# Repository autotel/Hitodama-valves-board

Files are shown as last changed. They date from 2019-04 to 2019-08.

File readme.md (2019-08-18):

# to fix:
* ---Teensy-board, connect VCC to teensy 3v---
* ---caps wrong way around in valves boards.---
* ---check about the twistedness of the ribbon cable---

* Cannot use the DAC pins (A21,A22) as digital!

board to control two valves and two pressure sensors from microcontroller.

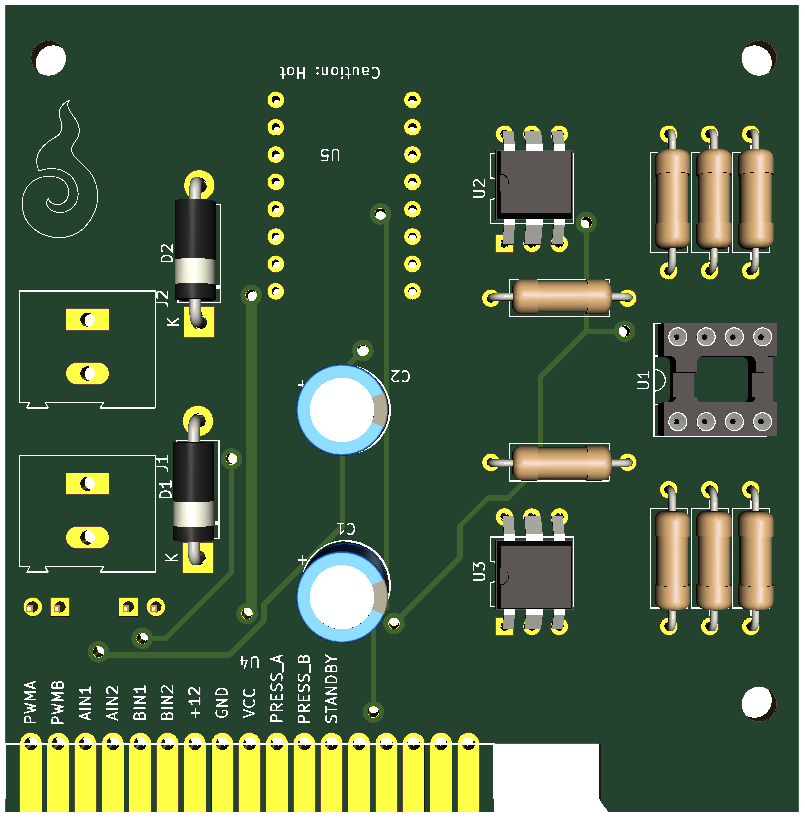
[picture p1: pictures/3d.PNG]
render


Electronic design: Avner Peled & Joaquín Aldunate

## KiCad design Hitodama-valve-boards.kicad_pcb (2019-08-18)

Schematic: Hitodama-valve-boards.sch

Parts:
C1, C2: 100uF 25v; CP_Radial_D8.0mm_P3.80mm
D1, D2: D; D_5W_P12.70mm_Horizontal
H1, H2, H3, H4: MountingHole; MountingHole_3.2mm_M3
J1: Solenoid A; TerminalBlock_Altech_AK300-2_P5.00mm
J2: Solenoid B; TerminalBlock_Altech_AK300-2_P5.00mm
JP1, JP2: (A,B)IN 1; PinHeader_1x02_P2.54mm_Vertical
R1, R5: 80K; R_Axial_DIN0309_L9.0mm_D3.2mm_P12.70mm_Horizontal
R2, R6: 10K; R_Axial_DIN0309_L9.0mm_D3.2mm_P12.70mm_Horizontal
R3, R7: 3.3K; R_Axial_DIN0309_L9.0mm_D3.2mm_P12.70mm_Horizontal
R4, R8: 33K; R_Axial_DIN0309_L9.0mm_D3.2mm_P12.70mm_Horizontal
U1: LM358; DIP-8_W7.62mm_Socket_LongPads
U2: Pressure_b; DIP-6_W10.16mm
U3: Pressure_a; DIP-6_W10.16mm
U4: ChamberBoard_Holder; chamber_board_holder_ 5-5530843-3_male
U5: Pololu-713; pololu713

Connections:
+12V: U4.7, U5.7
/A.IN.1: JP1.1, U4.3, U5.14
/A.IN.2: U4.4, U5.15
/A.PRESSURE: R8.1, U1.1, U4.10
/A.PWM: JP2.2, U4.1, U5.16
/B.IN.1: JP1.2, U4.5, U5.12
/B.IN.2: U4.6, U5.11
/B.PRESSURE: R4.1, U1.7, U4.11
/B.PWM: JP2.1, U4.2, U5.10
/HVA+: D1.1 (K), J1.2, U5.3
/HVA-: D1.2 (A), J1.1, U5.4
/HVB+: D2.1 (K), J2.2, U5.6
/HVB-: D2.2 (A), J2.1, U5.5
/stby: U4.12, U5.13
GND: C1.2, C2.2, R1.1, R5.1, U1.4 (V-), U2.2, U3.2, U4.8, U5.1, U5.9
unnamed: R1.2, R2.2, U1.5 (+)
unnamed: R2.1, U2.4
unnamed: R3.1, R4.2, U1.6 (-)
unnamed: R3.2, U2.1, U2.6
unnamed: R5.2, R6.2, U1.3 (+)
unnamed: R6.1, U3.4
unnamed: R7.1, R8.2, U1.2 (-)
unnamed: R7.2, U3.1, U3.6
VCC: C1.1, C2.1, U1.8 (V+), U2.5, U3.5, U4.9, U5.2

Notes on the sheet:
Modular
Head

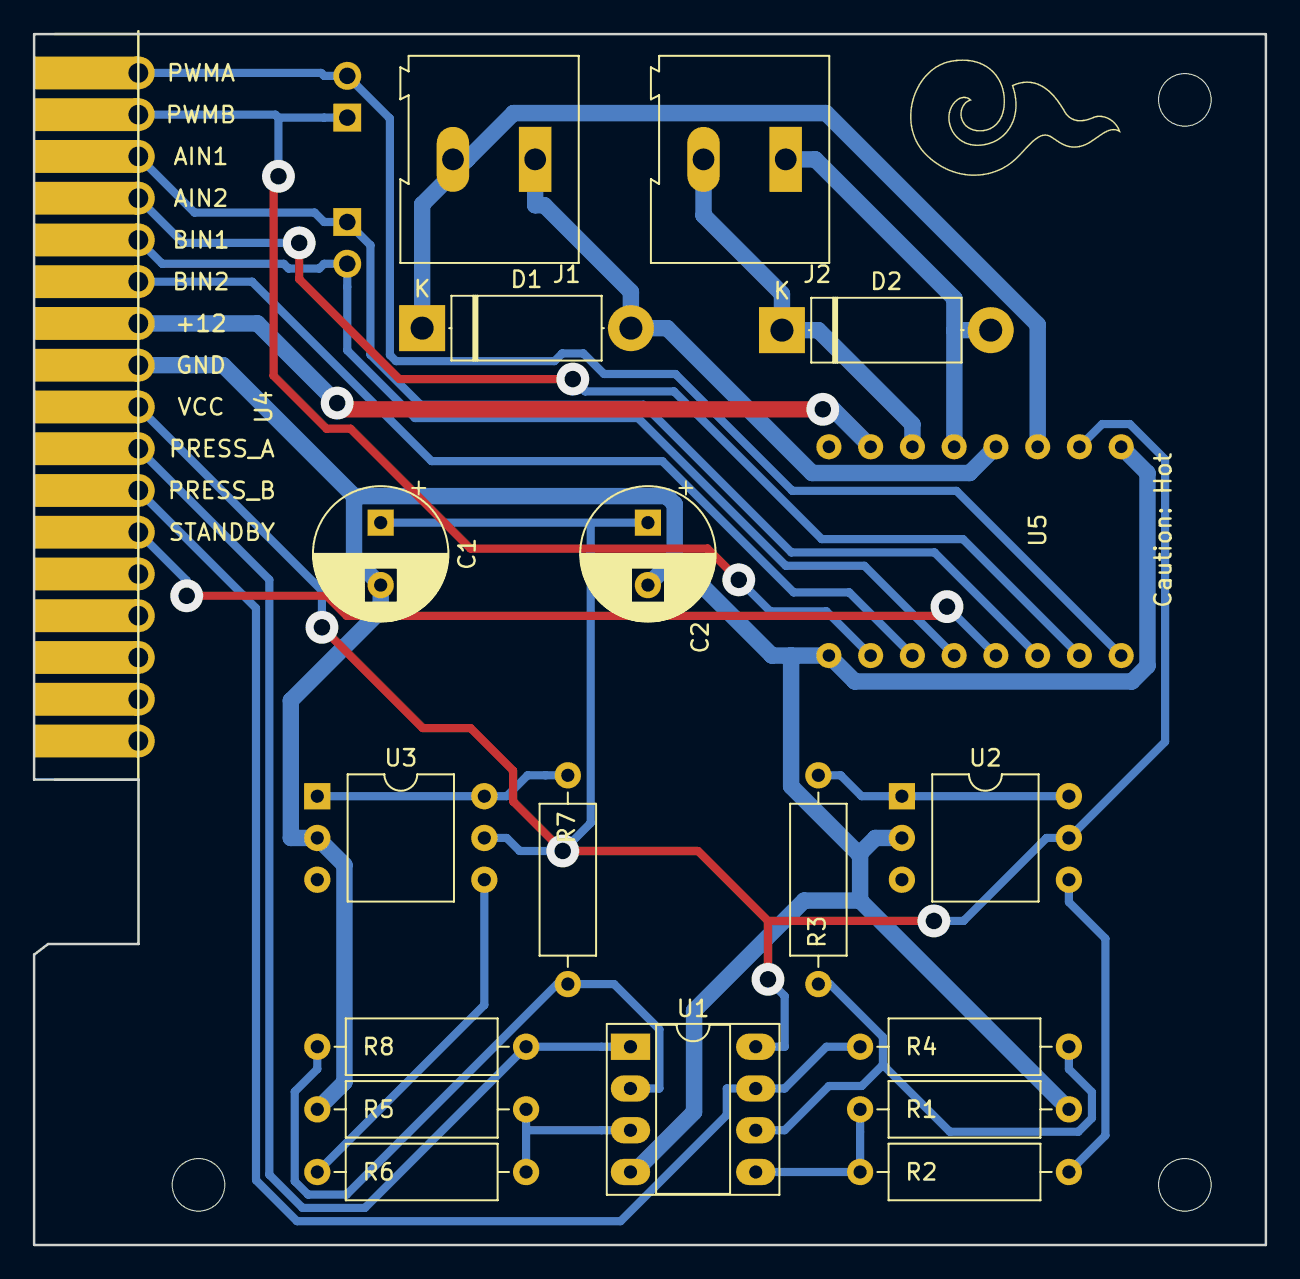
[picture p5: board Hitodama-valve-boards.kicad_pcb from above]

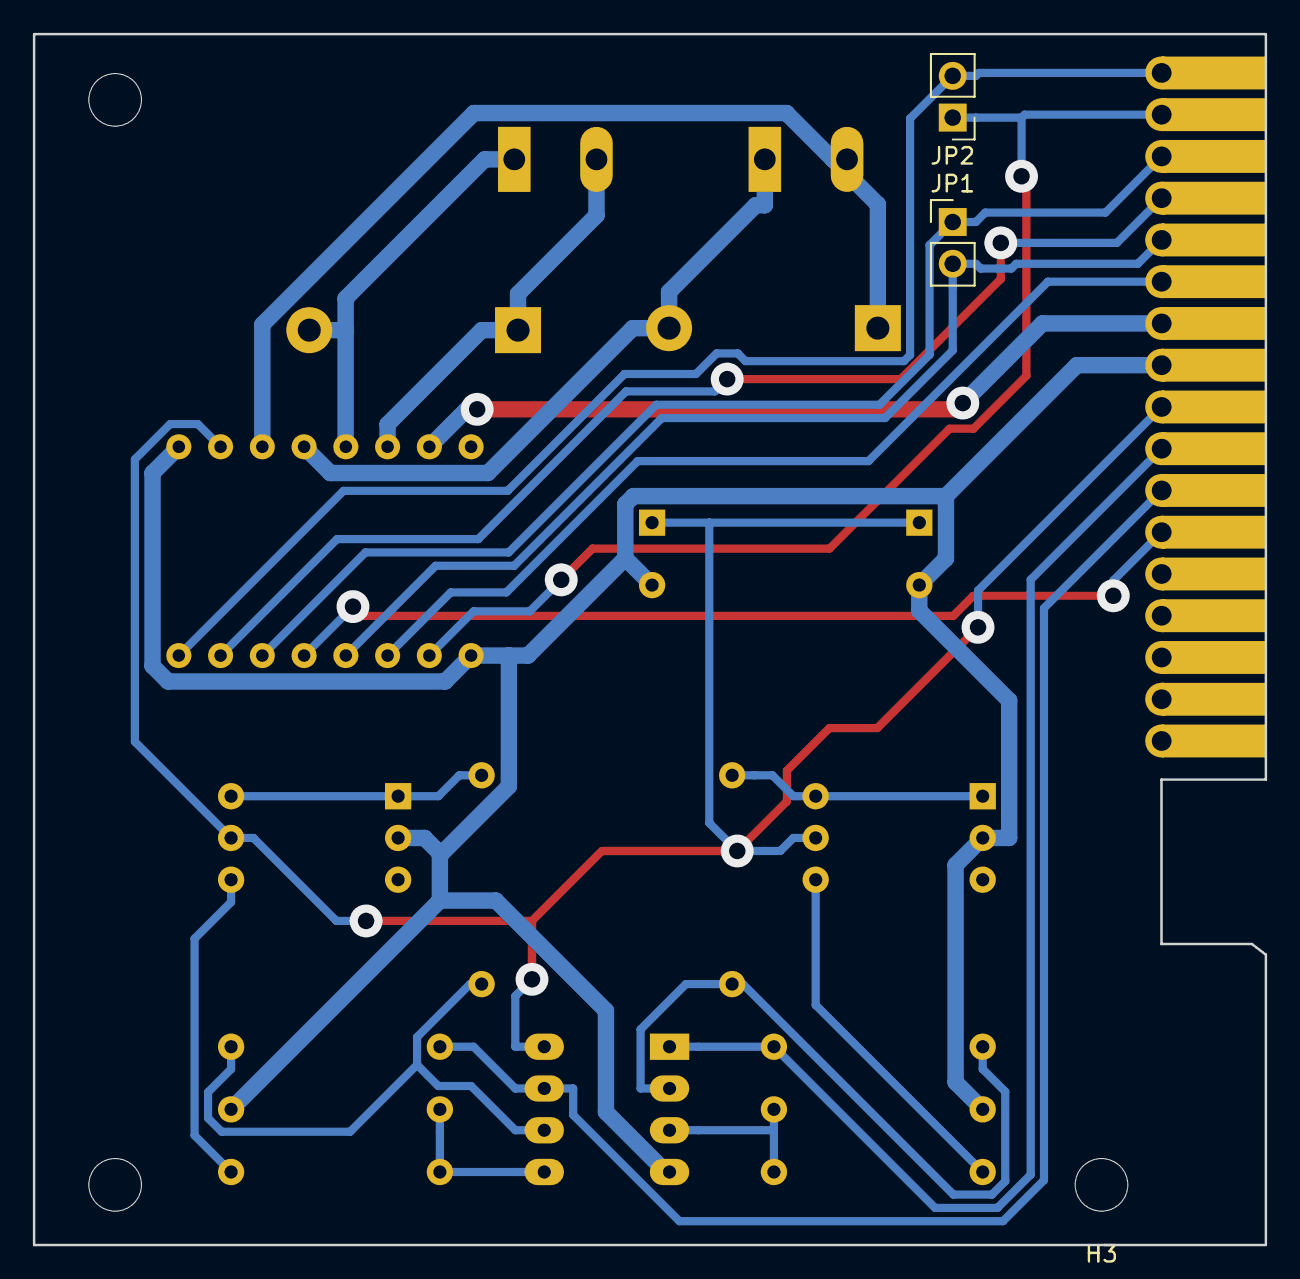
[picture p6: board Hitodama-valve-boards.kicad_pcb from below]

Board: 2 copper layers, 74.9 x 73.7 mm, 24 parts (4 on the bottom side), 24 nets.

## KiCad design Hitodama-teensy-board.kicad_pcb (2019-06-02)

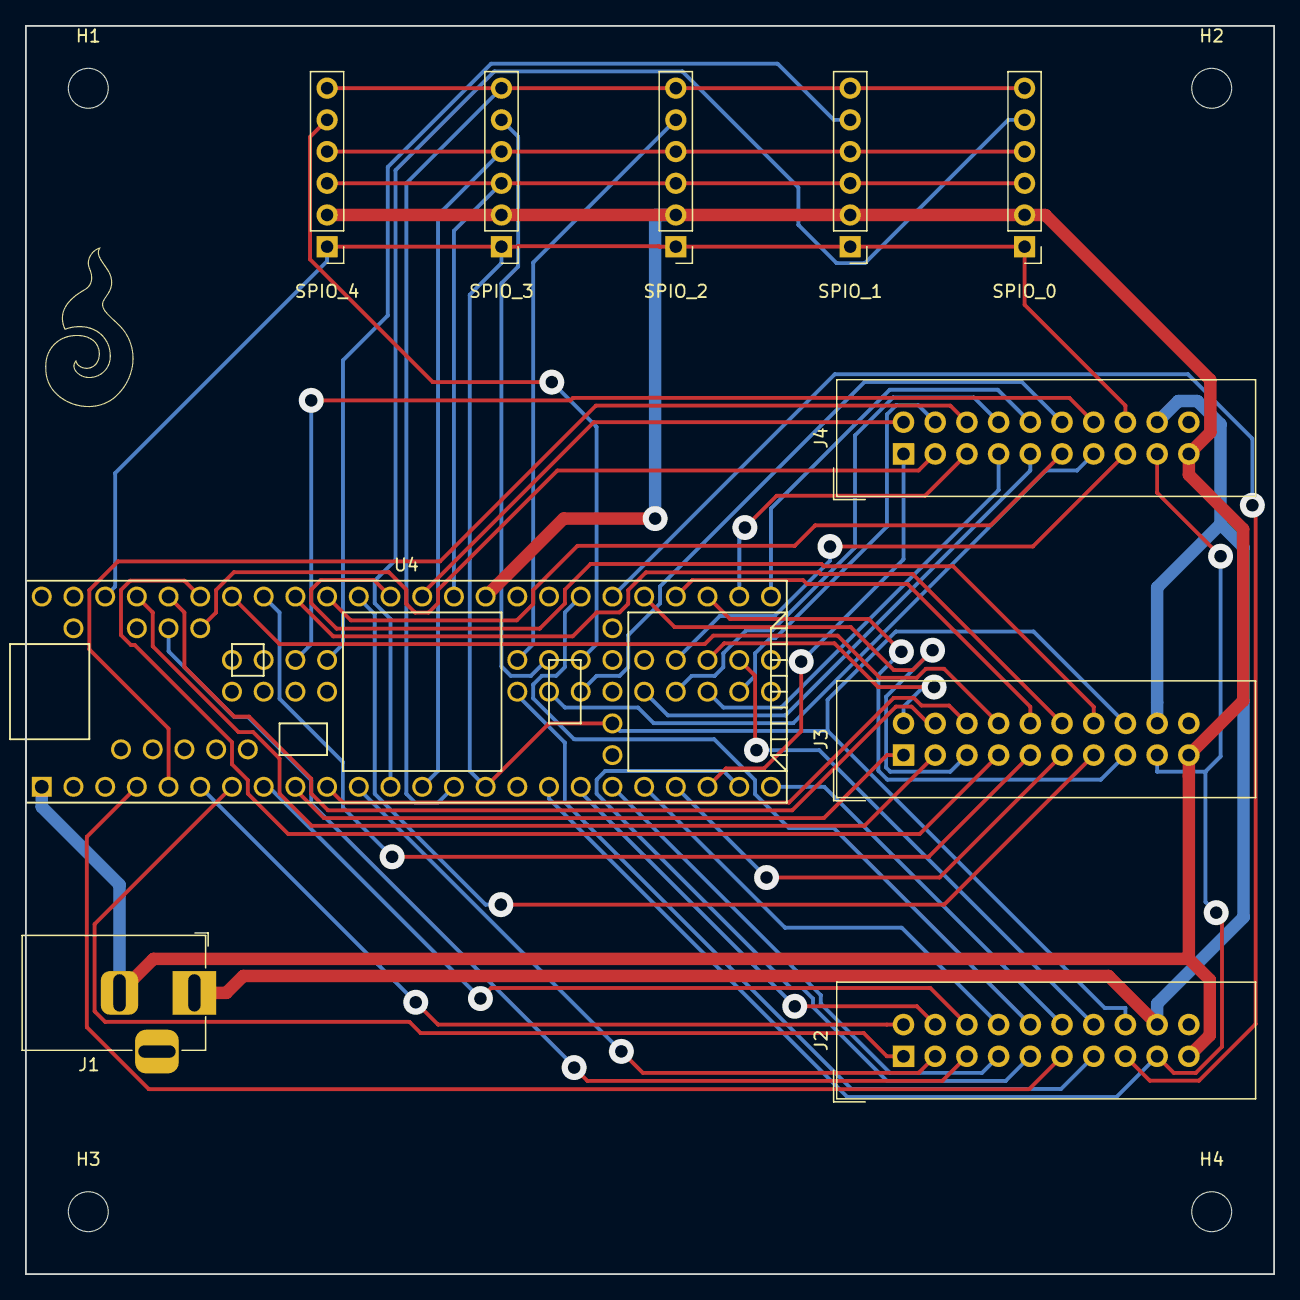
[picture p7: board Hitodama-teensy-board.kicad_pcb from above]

Board: 2 copper layers, 100.0 x 100.0 mm, 14 parts (0 on the bottom side), 57 nets.

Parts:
H1, H2, H3, H4: MountingHole; MountingHole_3.2mm_M3
J1: Jack-DC; BarrelJack_Horizontal
J2, J3, J4: Conn_01x20_Female; IDC-Header_2x10_P2.54mm_Vertical
SPIO_0, SPIO_1, SPIO_2, SPIO_3, SPIO_4: Conn_01x06_Female; PinHeader_1x06_P2.54mm_Vertical
U4: Teensy3.6; Teensy35_36

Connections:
+12V: J1.1, J2.18, J3.18, J4.18
/All.Stby: J2.17, J3.17, J4.17, U4.17
/ChamberA.ADC: J2.5, U4.56
/ChamberA.D1: J2.2, U4.6
/ChamberA.D2: J2.3, U4.11
/ChamberA.D3: J2.4, U4.18
/ChamberA.PWM: J2.1, U4.7
/ChamberB.ADC: J2.10, U4.36
/ChamberB.D1: J2.7, U4.19
/ChamberB.D2: J2.8, U4.20
/ChamberB.D3: J2.9, U4.23
/ChamberB.PWM: J2.6, U4.8
/ChamberC.ADC: J2.15, U4.35
/ChamberC.D1: J2.12, U4.24
/ChamberC.D2: J2.13, U4.67
/ChamberC.D3: J2.14, U4.76
/ChamberC.PWM: J2.11, U4.4
/ChamberD.ADC: J3.5, U4.34
/ChamberD.D1: J3.2, U4.77
/ChamberD.D2: J3.3, U4.50
/ChamberD.D3: J3.4, U4.49
/ChamberD.PWM: J3.1, U4.9
/ChamberE.ADC: J3.10, U4.33
/ChamberE.D1: J3.7, U4.48
/ChamberE.D2: J3.8, U4.47
/ChamberE.D3: J3.9, U4.46
/ChamberE.PWM: J3.6, U4.10
/ChamberF.ADC: J3.15, U4.32
/ChamberF.D1: J3.12, U4.45
/ChamberF.D2: J3.13, U4.43
/ChamberF.D3: J3.14, U4.42
/ChamberF.PWM: J3.11, U4.21
/ChamberG.ADC: J4.5, U4.31
/ChamberG.D1: J4.2, U4.41
/ChamberG.D2: J4.3, U4.57
/ChamberG.D3: J4.4, U4.73
/ChamberG.PWM: J4.1, U4.22
/ChamberH.ADC: J4.10, U4.30
/ChamberH.D1: J4.7, U4.72
/ChamberH.D2: J4.8, U4.71
/ChamberH.D3: J4.9, U4.70
/ChamberH.PWM: J4.6, U4.5
/ChamberI.ADC: J4.15, U4.78
/ChamberI.D1: J4.12, U4.69
/ChamberI.D2: J4.13, U4.68
/ChamberI.D3: J4.14, U4.84
/ChamberI.PWM: J4.11, U4.44
/SPI0.CS0: SPIO_0.5, U4.12
/SPI0.CS1: SPIO_1.5, U4.83
/SPI0.CS2: SPIO_2.5, U4.82
/SPI0.CS3: SPIO_3.5, U4.81
/SPI0.CS4: SPIO_4.5, U4.80
/SPI0.MISO: SPIO_0.6, SPIO_1.6, SPIO_2.6, SPIO_3.6, SPIO_4.6, U4.14
/SPI0.MOSI: SPIO_0.4, SPIO_1.4, SPIO_2.4, SPIO_3.4, SPIO_4.4, U4.13
/SPI0.SCK: SPIO_0.3, SPIO_1.3, SPIO_2.3, SPIO_3.3, SPIO_4.3, U4.40
GND: J1.2, J2.19, J3.19, J4.19, SPIO_0.2, SPIO_1.2, SPIO_2.2, SPIO_3.2, SPIO_4.2, U4.1, U4.39
VCC: J2.16, J3.16, J4.16, SPIO_0.1, SPIO_1.1, SPIO_2.1, SPIO_3.1, SPIO_4.1, U4.15, U4.26, U4.51

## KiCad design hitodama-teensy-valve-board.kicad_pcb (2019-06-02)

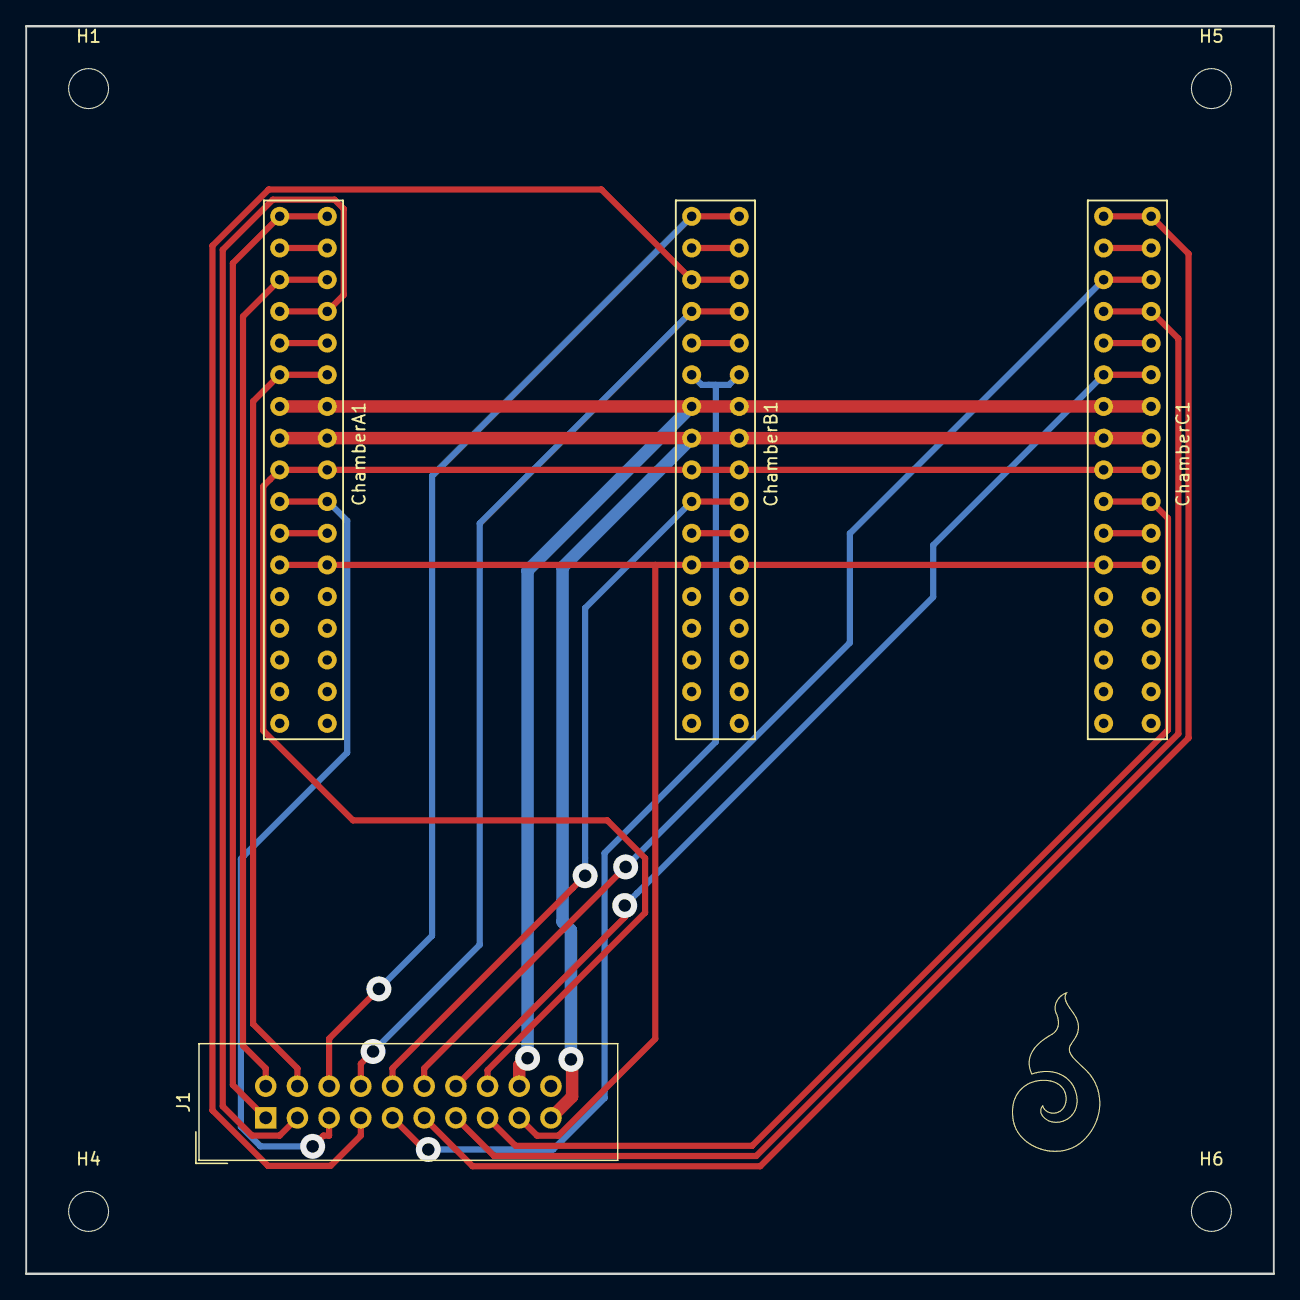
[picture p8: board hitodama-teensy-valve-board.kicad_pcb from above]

Board: 2 copper layers, 100.0 x 100.0 mm, 8 parts (0 on the bottom side), 19 nets.

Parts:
ChamberA1: ChamberBoard_Holder; 5-5530843-3 female
ChamberB1: ChamberBoard_Holder; 5-5530843-3 female
ChamberC1: ChamberBoard_Holder; 5-5530843-3 female
H1, H4, H5, H6: MountingHole; MountingHole_3.2mm_M3
J1: Conn_01x20_Female; IDC-Header_2x10_P2.54mm_Vertical

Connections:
+12V: ChamberA1.7, ChamberB1.7, ChamberC1.7, J1.18
/All.Stby: ChamberA1.12, ChamberB1.12, ChamberC1.12, J1.17
/ChamberA.ADC: ChamberA1.10, J1.5
/ChamberA.D1: ChamberA1.3, J1.2
/ChamberA.D2: ChamberA1.4, J1.3
/ChamberA.D3: ChamberA1.6, J1.4
/ChamberA.PWM: ChamberA1.1, J1.1
/ChamberB.ADC: ChamberB1.10, J1.10
/ChamberB.D1: ChamberB1.3, J1.7
/ChamberB.D2: ChamberB1.4, J1.8
/ChamberB.D3: ChamberB1.6, J1.9
/ChamberB.PWM: ChamberB1.1, J1.6
/ChamberC.ADC: ChamberC1.10, J1.15
/ChamberC.D1: ChamberC1.3, J1.12
/ChamberC.D2: ChamberC1.4, J1.13
/ChamberC.D3: ChamberC1.6, J1.14
/ChamberC.PWM: ChamberC1.1, J1.11
GND: ChamberA1.8, ChamberB1.8, ChamberC1.8, J1.19
VCC: ChamberA1.9, ChamberB1.9, ChamberC1.9, J1.16

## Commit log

2019-04-16 initial, demo board for chamber controller
    [Hitodama-valves-board.kicad_pcb, Hitodama-valves-board.sch]
2019-04-16 fixed capacitor colliding motor driver board
    [Hitodama-valves-board.kicad_pcb]
2019-04-16 improved adding +12v connector
    [Hitodama-valves-board.kicad_pcb, Hitodama-valves-board.sch]
2019-04-17 Change track definitions to fit Fablab's
    [Hitodama-valves-board.kicad_pcb]
2019-04-17 changed design rules for milling machine and consequently re-routed everyhting
    [Hitodama-valves-board.kicad_pcb, Hitodama-valves-board.sch]
2019-04-23 Separate the two board into different sch files. Added missing jumper (SCH only) and missing Vias for a jumber
    [Hitodama-teensy-board.kicad_pcb, Hitodama-teensy-board.sch, Hitodama-valve-boards.kicad_pcb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]
2019-04-23 Label all valve&motor controlle pins @ teensy
    [Hitodama-teensy-board.sch]
2019-04-23 Coordinate Connectors on both boards
    [Hitodama-teensy-board.kicad_pcb, Hitodama-teensy-board.sch, Hitodama-valve-boards.kicad_pcb]
2019-04-23 (auto) routing
    [Hitodama-teensy-board.dsn, Hitodama-teensy-board.kicad_pcb, Hitodama-valve-boards.dsn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]
2019-04-25 push some paths around
    [Hitodama-teensy-board.kicad_pcb]
2019-04-26 schematic add SPI ports & 12 v power connector
    [Hitodama-teensy-board.kicad_pcb, Hitodama-teensy-board.sch]
2019-04-26 route & DRC teensy board
    [Hitodama-teensy-board.dsn, Hitodama-teensy-board.kicad_pcb]
2019-04-30 separated the teensy board into four modules, so that it fits in smaller PCB's. Improved the chamber board, and added rules so that auto-router can figure out the optimal 1 layer+jumpers route
    [Hitodama-teensy-board.dsn, Hitodama-teensy-board.kicad_pcb, Hitodama-teensy-board.sch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]
2019-05-02 teensy board change 21 pins headers into 20 pins headers.
    [Hitodama-teensy-board.dsn, Hitodama-teensy-board.kicad_pcb, Hitodama-teensy-board.sch]
2019-05-03 fixed forgotten swap of pin headers on teensy-valves-board bridge
    [hitodama-teensy-valve-board.dsn, hitodama-teensy-valve-board.kicad_pcb, hitodama-teensy-valve-board.sch]
2019-05-13 2 row connector, routed on intermediate board
    [Hitodama-teensy-board.dsn, Hitodama-teensy-board.kicad_pcb, Hitodama-teensy-board.sch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]
2019-05-14 even greater trace widths
    [Hitodama-valve-boards.dsn, Hitodama-valve-boards.kicad_pcb, hitodama-teensy-valve-board.dsn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]
2019-05-20 fix misaligned hole
    [hitodama-teensy-valve-board.kicad_pcb]
2019-05-21 trying different routing options teensy board
    [Hitodama-teensy-board.kicad_pcb, Hitodama-teensy-board.sch, hitodama-teensy-board-1side.dsn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]
2019-05-30 fix some mistakes
    [Hitodama-valve-boards.kicad_pcb, Hitodama-valve-boards.sch]
2019-05-30 Added HITODAMA logo footprint
2019-05-31 remove useless texts
    [Hitodama-valve-boards.kicad_pcb]
2019-05-31 generate seedstudio gerber files
    [Hitodama-valve-boards.kicad_pcb]
2019-06-02 fix cap wrong orientation & teensy vcc.
    [Hitodama-teensy-board.kicad_pcb, Hitodama-teensy-board.sch, Hitodama-valve-boards.kicad_pcb]
2019-06-02 reduce teensy board size to 100x100
    [Hitodama-teensy-board.dsn, Hitodama-teensy-board.kicad_pcb, hitodama-teensy-board-1side_0.5mm.dsn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]
2019-06-02 change connectors into edge connector 5-5530843-3, TE Connectivity
    [Hitodama-valve-boards.dsn, Hitodama-valve-boards.kicad_pcb, Hitodama-valve-boards.sch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]
2019-06-02 fix wrong adc pins in teensy board
    [Hitodama-teensy-board.dsn, Hitodama-teensy-board.kicad_pcb, Hitodama-teensy-board.sch]
2019-06-02 added logos
    [Hitodama-teensy-board.kicad_pcb, Hitodama-valve-boards.kicad_pcb, hitodama-teensy-valve-board.kicad_pcb]
2019-06-02 Merge branch 'joaquin' into HEAD
    # Conflicts:
    # Hitodama-teensy-board.kicad_pcb
    [Hitodama-teensy-board.kicad_pcb, Hitodama-teensy-board.sch]
2019-06-02 check merge
    [Hitodama-teensy-board.kicad_pcb]
2019-06-02 enable silkscreen teensy board
    [Hitodama-teensy-board.kicad_pcb]
2019-08-18 update pic. & fix cutout not being exactly closed.
    [Hitodama-valve-boards.kicad_pcb]
